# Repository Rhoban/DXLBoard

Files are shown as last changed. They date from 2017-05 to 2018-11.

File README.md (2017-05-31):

# Rhoban DXL Board

This communication board was designed and used by the Rhoban teams for
humanoid robots. It features:

* 3 separate dynamixel buses that can be used in parallel, compatible with
  both 3-pin and 4-pin
* A socket for a GY-85 IMU
* A socket for a Maple Mini controller (based on the Cortex-M3, 32 bit
  arm at 72Mhz)
* USB cable can be directly soldered on it
* GPIO that can be used for buttons or any other purposes

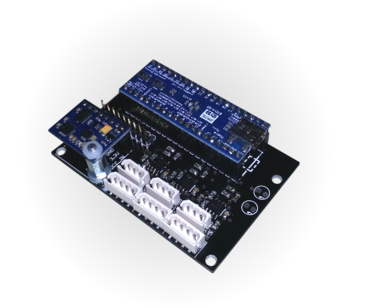
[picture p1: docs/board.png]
DXLBoard


## Documentation

Here you can find documentation about:

* [Electronics](/electronics/#electronics)
* [Mechanics](/mechanics/#mechanics)
* [Firmware](/firmware/#firmware)

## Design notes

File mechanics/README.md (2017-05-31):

# Mechanics

The board dimensions are depicted here:

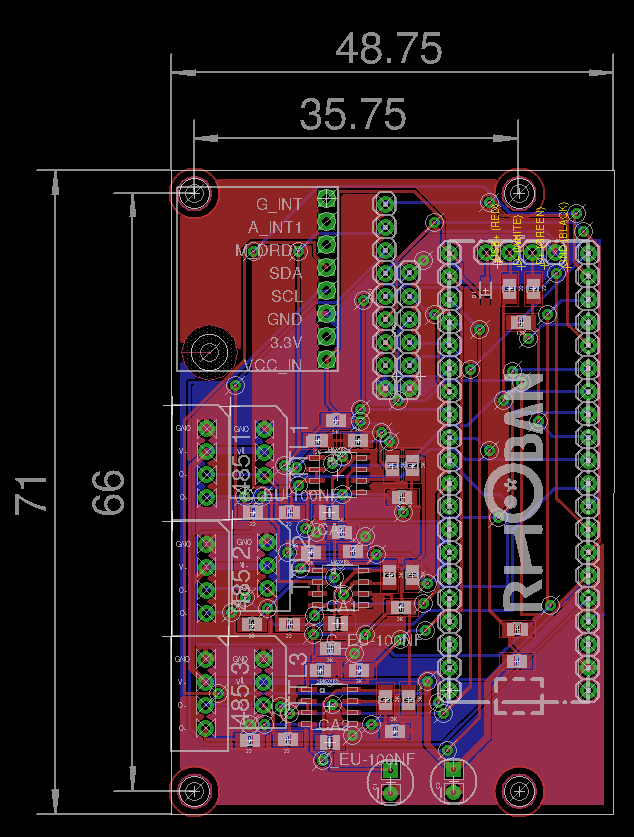
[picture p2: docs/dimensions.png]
Dimensions


## IMU

To get the IMU correctly fixed on the board, we recommend using
M3x12 female/male spacer, along with a M3x5 screw and a nylon nut.

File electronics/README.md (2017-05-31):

# Electronics

Here you'll find the schematic and (auto)routed board. You will need Eagle
to open the `.sch` and `.brd` files.

## Components

Here is a list of required components to build the board

Name               | Farnell ID | Quantity | Description
-------------------|------------|----------|--------------
2212S-20SG-85      | 1593469    | 2        | 1x20 0.1" female sockets for the Maple Mini
2212S-08SG-85      | 1593463    | 1        | 1x8 0.1" female socket for the IMU
MOLEX 22-03-5045   | 1104204    | 3        | Dynamixel 4 pins connector
MOLEX 22-03-5035   | 9979620    | 3        | Dynamixel 3 pins connector
ST485              | 1564306    | 3        | Buses transciever (can be replaced with MAX485), SOIC-8
R0805 22 ohms      | 2128982    | 8        | Protection resistors
R0805 1.5 Kohms    | 2129125    | 1        | USB detection resistor
R0805 2 Kohms      | 2129135    | 3        | Pull-up/Pull-down
R0805 3 Kohms      | 2129150    | 15       | Pull-up/Pull-down
C0805 100 nF       | 1759265RL  | 3        | Decoupling condensators
PMEG2005AEA        | 8737843RL  | 1        | Diode for on-board USB power supply
Maple mini      | N/A        | 1        | Controller board, featuring a 72Mhz 32-bit Cortex-M3 ARM controller
GY-85           | N/A        | 1        | 9 DOF IMU

## Powering

In the current version, the board is powered using 5V USB. You can use the mini
USB port from the Maple Mini, or solder wires to the USB part of the board (we
recommend doing that to have a better integration). There is protection diode
on the Maple Mini and on the board.

The motor power lines are connected, however the board is not designed to
handle current so you still have to build a separate hub if you want to
power servomotors. 

## Bus design

The ST485 transciever is used here for both RS485 and TTL versions. It can also
be replaced with MAX485 which is pin compatible.

22 ohms serie resistors are used for bus protections to avoid damaging transcivers from
the devices or the board in the case the bus would be driven simultaneously by both.

There is a pull-up on the A line and a the B line is pulled to 2.5V. 

When transmitting, the lines are driven by the ST485, A is the positive output and B
the negative. In this case, the A line acts exactly as the data line of a TTL device.

When receiving, if you are using only 3-pins TTL, the A line will be either 5V (for '1')
or 0V (for '0') and the B line will remain at 2.5V. In this case, the RS485 speficiation
is still respected, because A-B should be above 200mV to read a '1' and below -200mV to
read a '0'.

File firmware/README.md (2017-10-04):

# Firmware

Here is the Maple Mini firmware for the DXL Board, it is based on the
Rhoban fork of the LibMaple

## Building it

First, you will need the ARM cortex toolchain:

```
sudo apt-get install libstdc++-arm-none-eabi-newlib gcc-arm-none-eabi libnewlib-arm-none-eabi binutils-arm-none-eabi dfu-util
```

Then, run the following commands:

```
./prepare.sh
make
make install
```

`make install` will send the program to the board using the DFU maple bootloader.

## How does it works

The board will appear as a virtual serial port (typically `/dev/ttyACM0` on linux).
You can directly send dynamixel packet through it.

Note that we confgure our servos as following:

* Baudrate: 1000000
* Return delay to minimum
* Status return level to 1 (only answer READ and not on WRITE)

## Sync Read

To take advantage of the 3 buses, there is a pseudo Sync Read command implemented
in the controller.

Note that you'll have to configure your servos to have the smallest possible 
return delay time.

The mapping of what device is on which bus is done on-the-fly when a response
is received. Thus, you may want to ping each device at the begining to be sure
the mapping is OK (it's a good practice anyway to check that all the devices are
present).

If you want to read `N` bytes at address `A` from `M` motors, here is the instruction
packet:

ID             | Instruction | Length | Data
---------------|-------------|--------|---------------------------------
Broadcast      | `0x84`      | M+2    | `A`, `N`, `ID1`, `ID2` ... `IDM`

Then, the board will send regular read packets on the buses, in parallel. Currently,
the timeout for these reads is hard coded `650 µS`.

The response will then be:

ID             | Instruction | Length | Data
---------------|-------------|--------|---------------------------------
Broadcast      | `0x84`      | (1 + `N`) * `M`    | `STATUS1`, `DATA1` (`N` bytes), `STATUS2`, `DATA2` ... `STATUSM`, `DATAM`

The `STATUSX` byte is the error field from the motor respond. In case of timeout, this
value will be `0xFF`.

## Reading data from the IMU

The GY-85 IMU is accessed using I²C bus and the raw values can be retrieved the same
way you read from a dynamixel device.

The dynamixel model of the imu will be `350` and its ID is `241`.

To read the IMU, you should ask for 110 bytes from the `0x24` address. Here is what you
will receive:

Field           | Size             | Encoding   
----------------|------------------|--------------------------
Accelerometer X | 16 bits signed   | Values for the accelerometer (raw)
Accelerometer Y | 16 bits signed   | 
Accelerometer Z | 16 bits signed   | 
Gyrometer X     | 16 bits signed   | Values for the gyrometer (raw)
Gyrometer Y     | 16 bits signed   | 
Gyrometer Z     | 16 bits signed   | 
Magnetometer X  | 16 bits signed   | Values for the magnetometer (raw)
Magnetometer Y  | 16 bits signed   | 
Magnetometer Z  | 16 bits signed   | 
Sequence        | 32 bits unsigned | Sequence number

This block of data is repeated 5 times, because the values are stored in a circular
buffer. Thus, the higher sequence number is the more recent is data. Note that asking
many bytes from the IMU is not very costy in the timings because the data are
here pure USB (through serial emulator).

The circular buffer is used to ensure that you don't miss any packet, since dynamixel
is a master/slave protocol.

* [ADXL345](http://www.analog.com/media/en/technical-documentation/data-sheets/ADXL345.pdf): Values from the accelerometer are 256 LSB per `g`.

* [ITG-3200](https://www.sparkfun.com/datasheets/Sensors/Gyro/PS-ITG-3200-00-01.4.pdf) Values from the gyrometer are 14.375 LSB per `deg/s`. We recommend you also calibrate the offset for its 0 value to avoid drift.

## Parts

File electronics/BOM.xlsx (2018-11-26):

 |  |  | Rhoban DXLBoard BOM
Item # | *Ref Des | *Qty | Manufacturer | *Mfg Part # | Description / Value | *Package | Type | Your Instructions / Notes
1 | R1, R11, R12, R13, R14, R15, R17, R18, R19, R2, R20, R21, R23, R3, R4 | 15 | MULTICOMP | MCSR08X3001FTL | Resistor 3K | 0805 | SMD | Farnell : 2074431
2 | R5, R6, R7S1, R7S2, R8S, R8S1, R8S2, R8S3 | 8 | MULTICOMP | MCWR08X22R0FTL | Resistor 22 Ohms | 0805 | SMD | Farnell : 2446926
3 | R7 | 1 | MULTICOMP | MCWR08X1501FTL | Resistor 1.5K | 0805 | SMD | Farnell : 2447592
4 | R10, R16, R22 | 3 | MULTICOMP | MCWR08X2001FTL | Resistor 2K | 0805 | SMD | Farnell : 2447622
5 | R8 | 1 | MULTICOMP | MCSR08X1002FTL | Resistor 10K | 0805 | SMD | Farnell : 2074334RL
6 | R9 | 1 | MULTICOMP | MCSR08X1001FTL | Resistor 1K | 0805 | SMD | Farnell : 2074332RL
7 | CA, CA1, CA2 | 3 | MURATA | GCM21BR72A104KA37K | Capacitor 100nF | 0805 | SMD | Farnell : 2688486RL
8 | C1, C2 | 2 | RUBYCON | 25YXF47MEFC5X11 | Capacitor 47uF | Radial 5mm | Thru-Hole | Farnell : 1144619
9 | D1 | 1 | NEXPERIA | PMEG2005AEA | Diode Schottky | SOD-323 | SMD | Farnell : 8737843RL
10 | 485-1, 485-2, 485-3 | 3 | MOLEX | 22-03-5045 | Connector 4 pins | - | Thru-Hole | Farnell : 1104204
11 | TTL1, TTL2, TTL3 | 3 | MOLEX | 22-03-5035 | Connector 3 pins | - | Thru-Hole | Farnell : 9979620
12 | MAX1, MAX2, MAX485 | 3 | STMICROELECTRONICS | ST485BDR | Transceiver RS485 | SOIC8 | SMD | Farnell : 1564306
13 | U$6 | 1 | MULTICOMP | 2212S-08SG-85 | 0.1’’ female header, 8 pins | - | Thru-Hole | Farnell : 1593463
14 | MAPLE | 2 | MULTICOMP | 2212S-20SG-85 | 0.1’’ female header, 20 pins | - | Thru-Hole | Farnell : 1593469
Click for Instructions on How to Create a BOM (https://www.pcbway.com/blog/PCB_Assembly/How_to_Build_a_BOM__Bill_Of_Materials_.html)

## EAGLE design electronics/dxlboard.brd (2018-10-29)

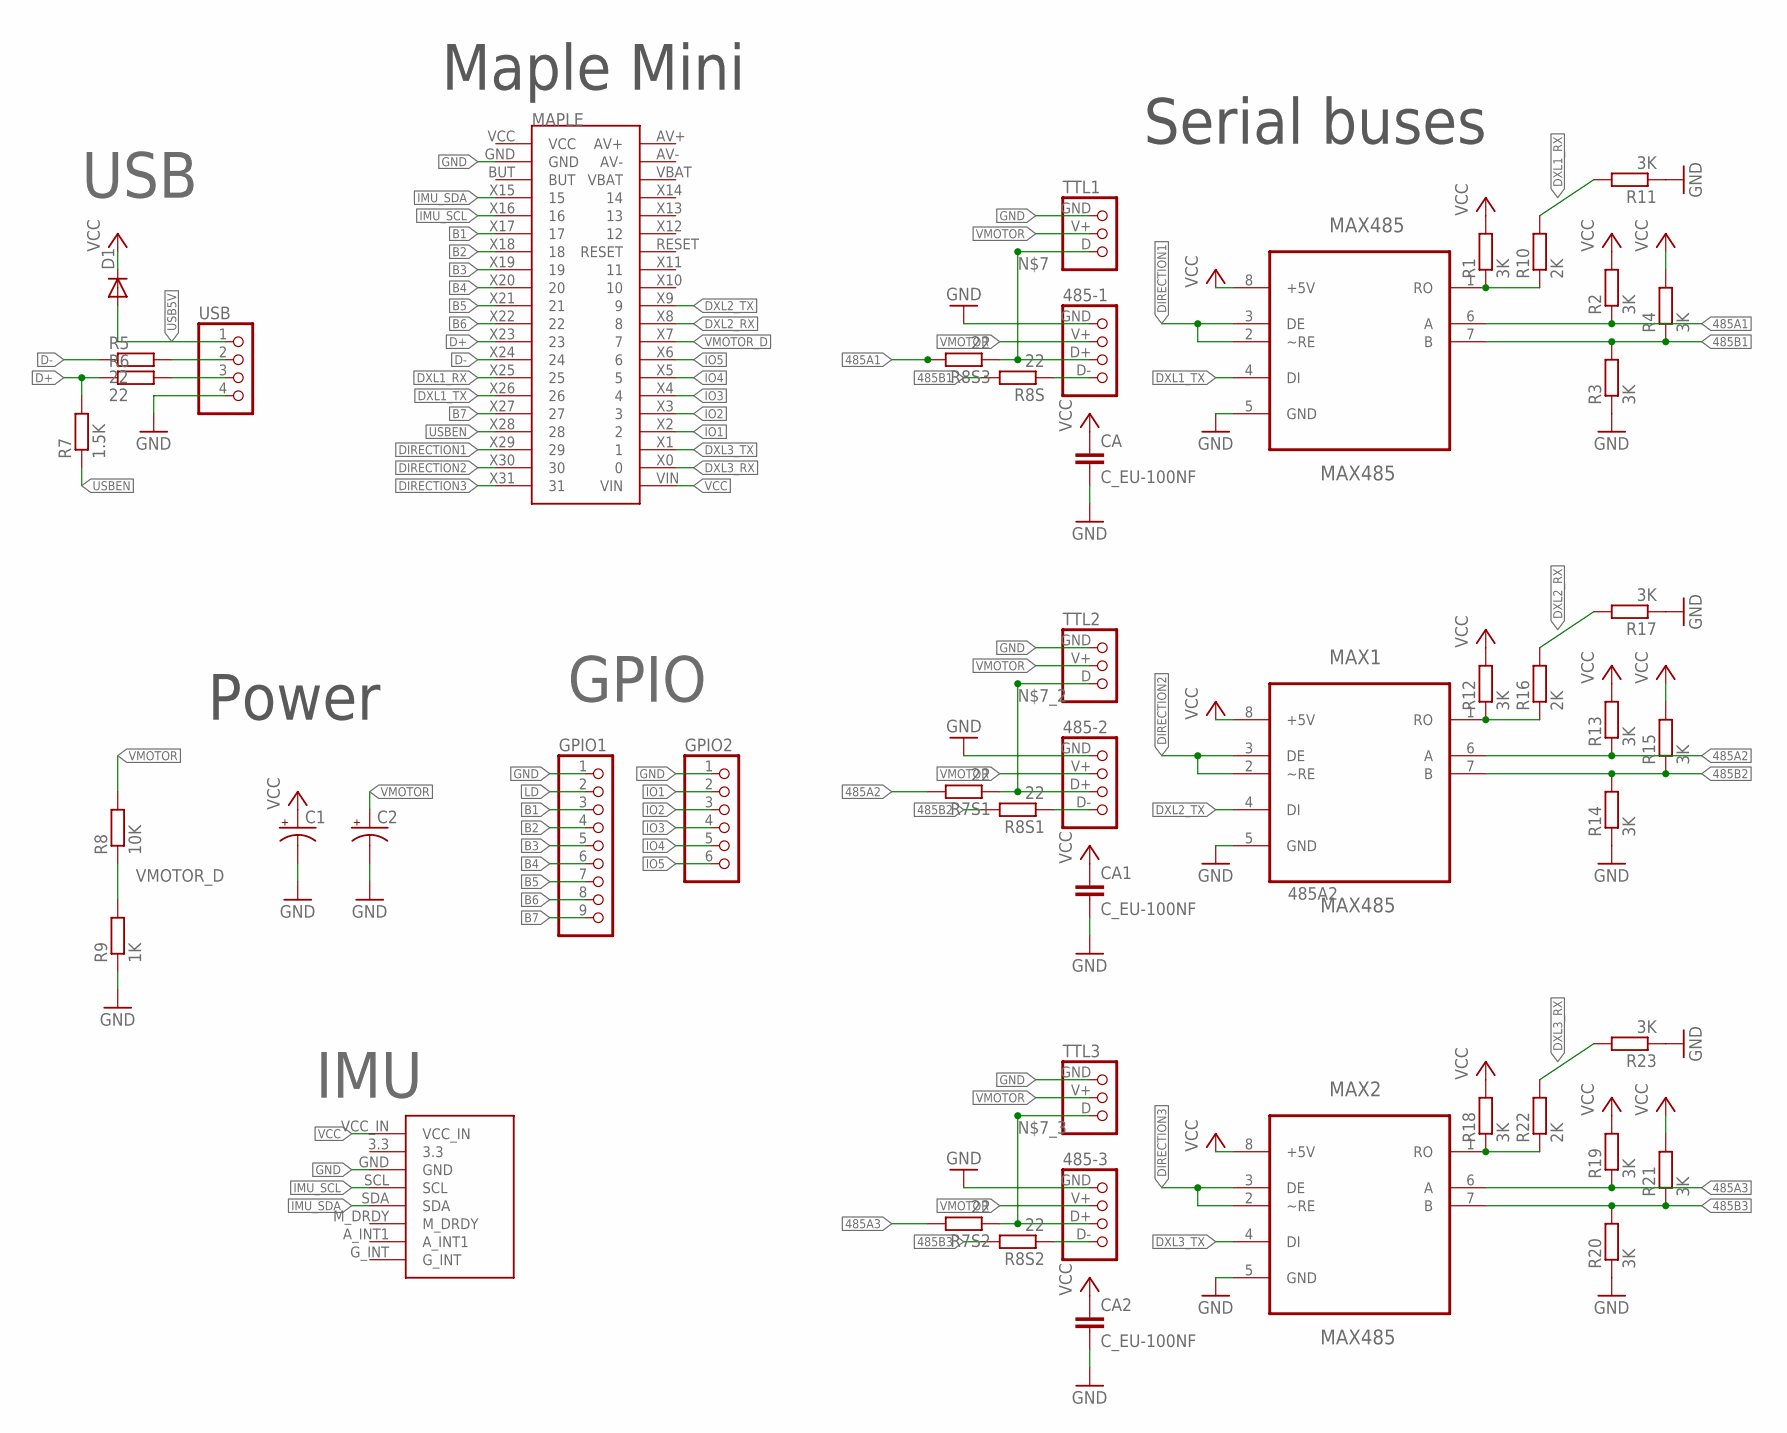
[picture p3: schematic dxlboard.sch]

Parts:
485-1, 485-2, 485-3: CONNEC_1X04_485; CONNEC_485; FARNELL 1104204
C1, C2: CAP_POLPTH2; CPOL-RADIAL-10UF-25V; FARNELL 1144619
CA, CA1, CA2: C_EU-100NF; C0805; FARNELL 2688486RL
D1: DIODESOD; SOD-323; FARNELL 8737843RL
GPIO1: CONNEC_1X09
GPIO2: CONNEC_1X06
MAPLE: MAPLE_MINI; CONNEC_2X20; FARNELL 1593469,1593469
MAX1, MAX2, MAX485: MAX485; SO8; FARNELL 1564306
R1, R2, R3, R4, R11, R12, R13, R14, R15, R17, R18, R19, R20, R21, R23: 3K; R0805; FARNELL 2074431
R5, R6, R7S1, R7S2, R8S, R8S1, R8S2, R8S3: 22; R0805; FARNELL 2446926
R7: 1.5K; R0805; FARNELL 2447592
R8: 10K; R0805; FARNELL 2074334RL
R9: 1K; R0805; FARNELL 2074332RL
R10, R16, R22: 2K; R0805; FARNELL 2447622
TTL1, TTL2, TTL3: CONNEC_1X03_TTL; CONNEC_TTL; FARNELL 9979620
U$6: GY-85; FARNELL 1593463
USB: CONNEC_1X04

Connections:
485A1: MAX485.6 (A), R2.1, R8S3.2
485A2: MAX1.6 (A), R7S1.2, R13.1
485A3: MAX2.6 (A), R7S2.2, R19.1
485B1: MAX485.7 (B), R3.2, R4.1, R8S.2
485B2: MAX1.7 (B), R8S1.2, R14.2, R15.1
485B3: MAX2.7 (B), R8S2.2, R20.2, R21.1
B1: GPIO1.3, MAPLE.X17 (17)
B2: GPIO1.4, MAPLE.X18 (18)
B3: GPIO1.5, MAPLE.X19 (19)
B4: GPIO1.6, MAPLE.X20 (20)
B5: GPIO1.7, MAPLE.X21 (21)
B6: GPIO1.8, MAPLE.X22 (22)
B7: GPIO1.9, MAPLE.X27 (27)
D+: MAPLE.X23 (23), R6.1, R7.2
D-: MAPLE.X24 (24), R5.1
DIRECTION1: MAPLE.X29 (29), MAX485.2 (~RE), MAX485.3 (DE)
DIRECTION2: MAPLE.X30 (30), MAX1.2 (~RE), MAX1.3 (DE)
DIRECTION3: MAPLE.X31 (31), MAX2.2 (~RE), MAX2.3 (DE)
DXL1_RX: MAPLE.X25 (25), R10.2, R11.2
DXL1_TX: MAPLE.X26 (26), MAX485.4 (DI)
DXL2_RX: MAPLE.X8 (8), R16.2, R17.2
DXL2_TX: MAPLE.X9 (9), MAX1.4 (DI)
DXL3_RX: MAPLE.X0 (0), R22.2, R23.2
DXL3_TX: MAPLE.X1 (1), MAX2.4 (DI)
DXL_1: MAX1.1 (RO), R12.1, R16.1
DXL_2: MAX2.1 (RO), R18.1, R22.1
DXL_485: MAX485.1 (RO), R1.1, R10.1
GND: 485-1.GND (1), 485-2.GND (1), 485-3.GND (1), C1.2 (-), C2.2 (-), CA.2, CA1.2, CA2.2, GPIO1.1, GPIO2.1, MAPLE.GND, MAX1.5 (GND), MAX2.5 (GND), MAX485.5 (GND), R3.1, R9.1, R11.1, R14.1, R17.1, R20.1, R23.1, TTL1.GND (1), TTL2.GND (1), TTL3.GND (1), U$6.GND, USB.4
IMU_SCL: MAPLE.X16 (16), U$6.SCL
IMU_SDA: MAPLE.X15 (15), U$6.SDA
IO1: GPIO2.2, MAPLE.X2 (2)
IO2: GPIO2.3, MAPLE.X3 (3)
IO3: GPIO2.4, MAPLE.X4 (4)
IO4: GPIO2.5, MAPLE.X5 (5)
IO5: GPIO2.6, MAPLE.X6 (6)
LD: GPIO1.2
unnamed: 485-2.D- (4), R8S1.1
unnamed: R6.2, USB.3
unnamed: 485-3.D- (4), R8S2.1
unnamed: 485-1.D- (4), R8S.1
unnamed: R5.2, USB.2
unnamed: 485-1.D+ (3), R8S3.1, TTL1.D (3)
unnamed: 485-2.D+ (3), R7S1.1, TTL2.D (3)
unnamed: 485-3.D+ (3), R7S2.1, TTL3.D (3)
USB5V: D1.2 (A), USB.1
USBEN: MAPLE.X28 (28), R7.1
VCC: C1.1 (+), CA.1, CA1.1, CA2.1, D1.1 (C), MAPLE.VIN, MAX1.8 (+5V), MAX2.8 (+5V), MAX485.8 (+5V), R1.2, R2.2, R4.2, R12.2, R13.2, R15.2, R18.2, R19.2, R21.2, U$6.VCC_IN
VMOTOR: 485-1.V+ (2), 485-2.V+ (2), 485-3.V+ (2), C2.1 (+), R8.2, TTL1.V+ (2), TTL2.V+ (2), TTL3.V+ (2)
VMOTOR_D: MAPLE.X7 (7), R8.1, R9.2

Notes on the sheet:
Serial buses
Power
Maple Mini
USB
GPIO
IMU

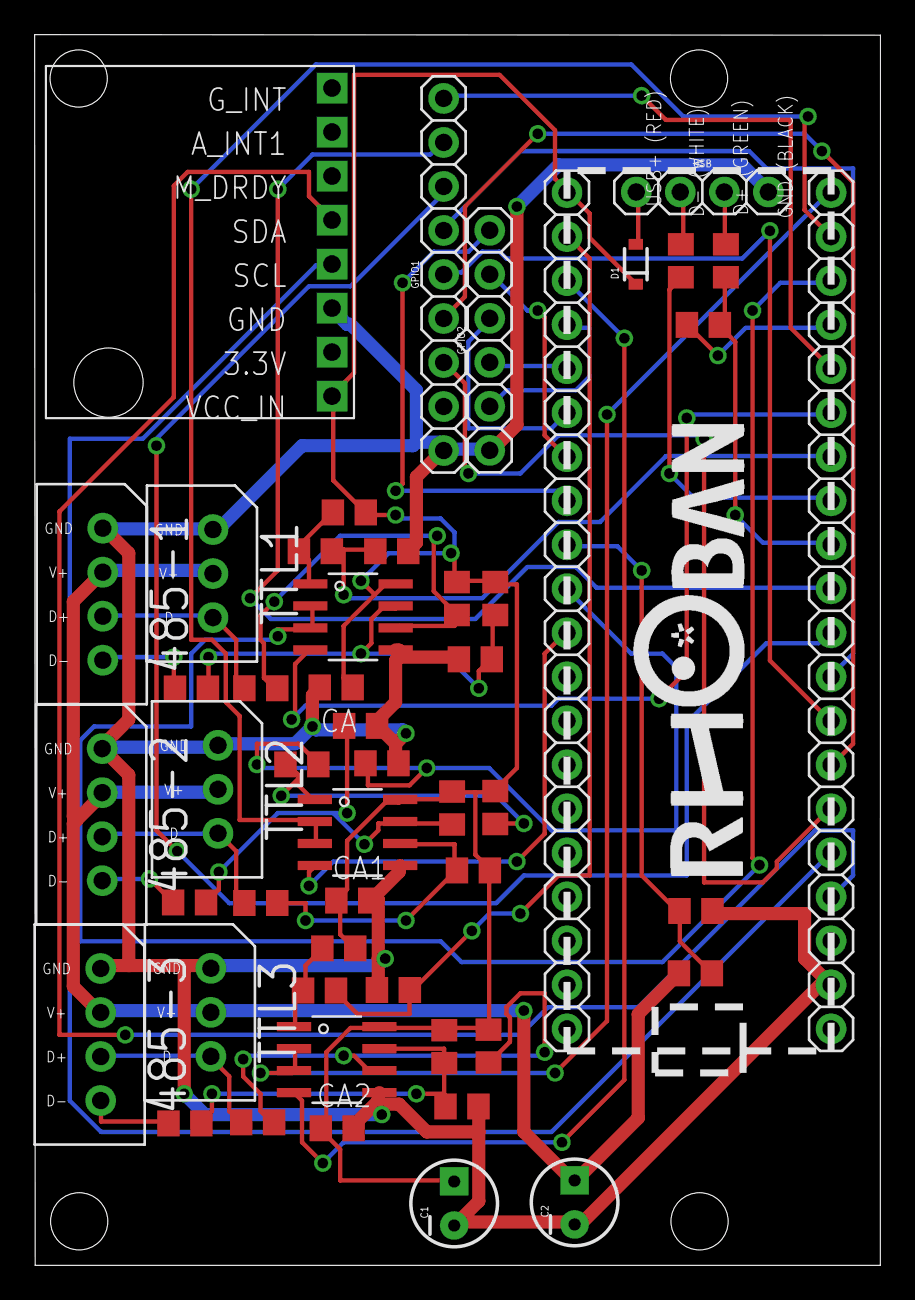
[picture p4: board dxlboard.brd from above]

Board: 2 copper layers, 48.8 x 71.0 mm, 53 parts (0 on the bottom side), 48 nets.

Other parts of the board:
U$2, U$3, U$4, U$5: STAND-OFF

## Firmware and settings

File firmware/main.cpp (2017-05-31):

#include <stdlib.h>
#include <stdio.h>
#include <math.h>
#include <wirish/wirish.h>
#include <libmaple/usart.h>
#include <Servo/Servo.h>
#include <gpio.h>
#include "dxl.h"
#include "dxl_usb_serial.h"
#include "dxl_servo.h"
#include "dxl_serial.h"
#include "dxl_magnetic_coder.h"
#include "dxl_gy85.h"
#include "dxl_pins.h"
    
struct dxl_bus bus;
volatile struct dxl_device dxl_usb_serial;
volatile struct dxl_device slaves[8];

void button()
{
    digitalWrite(BOARD_LED_PIN, HIGH);
}

void setup()
{ 
    int k = 0;

    // Enabling custom USB port
    pinMode(28, OUTPUT);
    digitalWrite(28, HIGH);

    //test();
    pinMode(BOARD_BUTTON_PIN, INPUT_PULLDOWN);
    pinMode(BOARD_LED_PIN, OUTPUT);
    digitalWrite(BOARD_LED_PIN, LOW);

    nvic_irq_set_priority(NVIC_USART1, 0x0);
    nvic_irq_set_priority(NVIC_USART2, 0x0);
    nvic_irq_set_priority(NVIC_USART3, 0x0);
    nvic_irq_set_priority(NVIC_DMA_CH2, 0x0);
    nvic_irq_set_priority(NVIC_DMA_CH4, 0x0);
    nvic_irq_set_priority(NVIC_DMA_CH7, 0x0);

    attachInterrupt(BOARD_BUTTON_PIN, button, RISING);

    dxl_bus_init(&bus);

    // The master of the bs is the usb serial emulator
    dxl_usb_serial_init(&dxl_usb_serial);
    dxl_set_master(&bus, &dxl_usb_serial);

    // Adding servo pin 15 to dynamixel id 220, and pin 16 to id 221
    // dxl_servo_init(&slaves[k++], 15, 220);
    // dxl_servo_init(&slaves[k++], 16, 221);
    
    // Add the Serial-forward dynamixel device as a slave
    dxl_serial_init(&slaves[k++], 1);
    dxl_serial_init(&slaves[k++], 2);
    dxl_serial_init(&slaves[k++], 3);

    // Add the ADC dynamixel on the bus, id 240
    // dxl_adc_init(&slaves[k++], 240);

    // Add the IMU dynamixel, id 241, port Serial2
    dxl_gy85_init(&slaves[k++], 241, I2C1);

    // Adding pins
    dxl_pins_init(&slaves[k++], 242);
    
    // Add a magnetic coder on the bus, ID 235
    // dxl_magnetic_coder_init(&slaves[k++], 3, 235);

    // Add an ADC coder on the bus, ID 235
    // dxl_coder_init(&slaves[k++], 3, 4, 5, 235);
   
    // Adding all slaves on the b us
    for (k--; k>=0; k--) {
        dxl_add_slave(&bus, &slaves[k]);
    }
}

void loop()
{
    dxl_bus_tick(&bus);
}

// Force init to be called *first*, i.e. before static object allocation.
// Otherwise, statically allocated objects that need libmaple may fail.
__attribute__((constructor)) void premain()
{
    init();
}

int main(void)
{
    setup();

    while (true) {
        loop();
    }
    return 0;
}

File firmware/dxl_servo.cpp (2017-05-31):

#include <stdlib.h>
#include <wirish/wirish.h>
#include <string.h>
#include "dxl_servo.h"
#include "dxl_protocol.h"

struct dxl_servo_private 
{
    ui8 pin;
    struct dxl_registers registers;
};

static bool dxl_servo_check_id(volatile struct dxl_device *self, ui8 id)
{
    volatile struct dxl_servo_private *data = (volatile dxl_servo_private *)self->data;
    return (id == data->registers.eeprom.id);
}

static void dxl_servo_write_data(volatile struct dxl_device *self, ui8 id, ui8 addr, ui8 *values, ui8 length)
{
    int oldTorque;
    volatile struct dxl_servo_private *data = (volatile dxl_servo_private *)self->data;
    
    oldTorque = data->registers.ram.torqueLimit;

    memcpy(((ui8 *)(&data->registers))+addr, values, length);

    if (oldTorque < data->registers.ram.torqueLimit) {
        data->registers.ram.torqueEnable = 1;
    }

    if (!data->registers.ram.torqueEnable) {
        data->registers.ram.torqueLimit = 0;
    }
    
    if (data->registers.ram.torqueLimit > 0) {
        pwmWrite(data->pin, data->registers.ram.goalPosition*8);
    } else {
        pwmWrite(data->pin, 0);
    }
}

static void dxl_servo_read_data(volatile struct dxl_device *self, ui8 id, ui8 addr, ui8 *values, ui8 length, ui8 *error)
{
    volatile struct dxl_servo_private *data = (volatile dxl_servo_private *)self->data;

    data->registers.ram.presentPosition = data->registers.ram.goalPosition;

    memcpy(values, ((ui8*)&data->registers)+addr, length);
    *error = 0;
}

static void dxl_servo_process(volatile struct dxl_device *self, volatile struct dxl_packet *packet)
{
    dxl_process(self, packet, dxl_servo_check_id, dxl_servo_write_data, dxl_servo_read_data);
}

static void dxl_servo_init_timers()
{
    HardwareTimer timer(4);
    timer.pause();
    timer.setPrescaleFactor(SERVOS_TIMERS_PRESCALE);
    timer.setOverflow(SERVOS_TIMERS_OVERFLOW);
    timer.refresh();
    timer.resume();
}

void dxl_servo_init(volatile struct dxl_device *device, ui8 pin, ui8 id)
{
    static bool timers_inited = false;

    if (!timers_inited) {
        timers_inited = true;
        dxl_servo_init_timers();
    }

    volatile struct dxl_servo_private *data = (volatile struct dxl_servo_private *)malloc(sizeof(struct dxl_servo_private));
    dxl_device_init(device);
    device->process = dxl_servo_process;
    device->data = (void *)data;

    data->registers.eeprom.modelNumber = DXL_SERVO_TYPE;
    data->registers.eeprom.firmwareVersion = 1;
    data->registers.eeprom.id = id;
    data->registers.ram.presentPosition = 0;
    data->registers.ram.goalPosition = 0;
    data->registers.ram.torqueEnable = 0;
    data->registers.ram.torqueLimit = 0;
    data->pin = pin;

    pinMode(pin, PWM);
    pwmWrite(pin, 0);
}

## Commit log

2017-06-05 IMU ID
2018-02-05 Adding Farnell attributes
    [dxlboard.brd, dxlboard.sch]
2018-03-10 Errors check in gy85
    [gy85.cpp]
2018-08-30 Switching labels to XRef
    [dxlboard.sch]
2018-08-30 Updating FARNELL attributes & making BOM
    [BOM.xlsx, dxlboard.brd, dxlboard.sch]
2018-08-30 Fixing item #
    [BOM.xlsx]
2018-10-29 gerber files

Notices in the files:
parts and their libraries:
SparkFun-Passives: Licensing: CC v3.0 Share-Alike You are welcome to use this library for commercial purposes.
